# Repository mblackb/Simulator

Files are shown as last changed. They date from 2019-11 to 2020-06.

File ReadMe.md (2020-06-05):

# Documentation for Elcano Simulator Code

**UW Bothell, 2020**

**Advisor :** *Tyler Folsom*

**Team 2019:** *Zach Gale, Jonah Lim, Matthew Moscola, Francisco Navarro-Diaz*

**Team 2020:** *Colton Sellers, Brandon Thompson, Mariah Files, Will Song, Launnie Ginn*

## Purpose
The following is a generalized list of the desired functionality of the simulator.
 - Simulate data for all sensors associated with Elcano Trike.
 - Simulate Elcano behavior to throttle, brake, and steering.
 - Have low and high-level boards function normally with the simulated sensor data without knowing data is being simulated.
 - Allow low and high-level board interaction to be tested.
 - Allow autonomous driving to be tested.
 
## Components ##

#### Simulation:
Code to be executed by a computer that has access to a Carla server, either locally, or through a network.  Controls all objects in Carla simulation.  Sends data to routerboard via client.  Also retrieves actuation instructions from the router board and sends to Carla to control the vehicle.

#### Router Board:
Code to be executed on the Arduino Due that functions as the router board.  Routes drive commands from low-level to Carla.  Also routes sensor data from Carla to high/low-level boards.

## How to Set-Up ##
The following is a guide to set up the Elcano simulator.

#### Materials: 
- 2 Arduino Due. (1 with High-Level Code, 1 with router board code)
- 1 Low-level board with Arduino Mega 2560.
- 1 Router board PCB (Schematics Included, created for Elcano Project)
- 1 male to female DB15 ribbon cable.
- 2 USB A male to USB Micro B male cables.
- 1 USB A male to B male cable.
- 1 computer running Carla 0.9.8 (Can run locally, for development we do this)
- 1 computer to interface between Carla client (Our Simulation Client) and router board (Using Due Router Board Programming Port)

#### To get the Repo as well as submodules (High level and Low level code)
Use git in a shell to clone the repo into a directory using the options below
OR
Just download the repo as zip and unpack (Ensure you have the high level and low level code in the arduino dir)

#### Option 1: clone, then update submodules (If you don't need the arduino code, just clone)
git clone https://github.com/C-SELLERS/Simulator

cd .\Simulator\

git submodule init

git submodule update

#### Option 2: Get repo and recursively get submodules
git clone https://github.com/C-SELLERS/Simulator --recursive

#### Arduino Preparation (If uploading arduino code)
Libraries needed are listed below:

- CAN_BUS_SHIELD by Seeed-Studio
  - [https://github.com/Seeed-Studio/CAN_BUS_Shield](https://github.com/Seeed-Studio/CAN_BUS_Shield)
- PID by Brett Beauregard
  - [https://github.com/br3ttb/Arduino-PID-Library](https://github.com/br3ttb/Arduino-PID-Library)
- Pin Change Interrupt by Nico Hood
  - [https://github.com/NicoHood/PinChangeInterrupt](https://github.com/NicoHood/PinChangeInterrupt)
- MCP48x2 DAC by Jonas Forsberg
  - [https://github.com/SweBarre/MCP48x2](https://github.com/SweBarre/MCP48x2).
- Arduino Due Timer Interrupts by Ivan Seidel
  - [https://github.com/ivanseidel/DueTimer](https://github.com/ivanseidel/DueTimer)

Then connect each arduino and upload the respective code to each board. 
   - HighLevel (./Arduino/HighLevel/) code to Arduino Mega (Right side of Router PCB)
   - LowLevel (./Ardunio/LowLevel/) code to Arduino Due (Left side of Router PCB)
   - Routerboard (./Arduino/Router_Board_v1) code to Arduino Due (Middle of Router PCB)

NOTE: PORTS ARE IMPORTANT ON ROUTERBOARD DUE
  - Programming port is used to upload code and debug via serial monitor
  - Native port is used to communicate with CARLA

#### Python Requirements:
- Have Python 3 Installed, we use (3.7.6)
- In a terminal move to .\Simulation\
- run: pip3 install -r requirements.txt
- Pip will install all the required python libraries for the simulator

#### Start Simulation:
- Make sure Carla is running either locally or somewhere accessible over the network
- If not already, have routerboard due plugged in via native port
- Start Simulator UI by running start.bat (.\Simulation\start.bat)
- By default it will populate local running Carla settings, if using a network based server enter IP and Port of Carla into the respective boxes. (i.e. 192.168.1.1, 2010)
- For control via Elcano leave mode as Auto, to control via manual keyboard input change mode to Manual.
- Click "Connect to CARLA"
   - If Auto mode, it will pop up selection of COM devices, select routerboard native port COM to begin and press go. (Will add path selection in the future???)
   - If Manual mode, client will start with keyboard controls (WASD) 

You did it!! Good job. :)

## Out of Scope Functionality Tested/Implemented ##
- Our project required us to delve into pieces of code within the Elcano project outside of our scope.  Understanding of how sensors are read by the high and low-level boards is necessary for the simulation of the sensors.  We were able to fix some issues regarding the CAN communication between the high and low-level boards.  The modified low-level code was not pushed to the main low-level code folder in the repository on Github, however, it is included within the simulator documentation.  The following were implemented.
- Unification of the proposed CAN message structure and the actual CAN message processing on the low-level code for CAN messages with ID 0x350 (High-level drive instructions).  These are CAN messages the high-level will send to the low level to facilitate autonomy.
- Fixing the DAC output voltage by using the MCP48x2 library by Jonas Forsberg.

## To Do (Software): ##
#### High Priority:
- Simulate gyro sensor
- Simulate accelerometer/magnetometer sensor.
- Simulate wheel angle sensor.
- Implement steering actuation when low-level CAN processing of steering command is fixed.
- Initialize CAN with high-level board code and incorporate in demo instead of separate CAN transceiver.
#### Medium Priority:
- Simulate ScanseSweep.
- Implement receiver board when board is fully fixed.
- Incorporate Elcano trike physics to simulated vehicle.
#### Low Priority

## Bugs
- While we were able to fix the code for the low-level CAN interpretation of the throttle and brake commands from high-level CAN messages, the PWM steering response was not fully tested.  We were unable to get the low-level board to output the correct PWM for the sent CAN messages and this needs more testing.
- The receiver board cannot get CAN to initialize.  Voltage testing confirmed that the CAN components (MCP2515 and MCP 2550) are receiving the correct operating voltages (5v).  Also, multiple CAN libraries besides the suggested Seeed Studio library were tested with no success (SparkFun CAN library was one of the tested libraries).  Possible problem is incompatibility between the 5v CAN components and the 3.3V SAMD21 board.  Another possible problem is design flaw of pcb.
- Low-level processing of CAN messages for ID 0x350 is faulty.  Bit shifting and produced output do not match the CAN guidelines on the wiki.  This was fixed in the low-level code included in the simulator folder but not pushed to the Elcano Github repository.

## Note:
- In PowerShell, in CarlaUE4 path, run Carla as: ***Start-Process CarlaUE4 -ArgumentList “—quality-level=Low”*** to lower gpu load.
- Headless mode can be enabled for complete removal of graphics rendering, however, visual debugging is extremely useful.

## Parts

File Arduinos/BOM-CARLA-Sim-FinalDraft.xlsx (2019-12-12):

Part
Build Qty | Unit Price | Order Qty | Ext Price | Value | Device | Package | Parts | Description | DigiKey Part Number | Manufactorer Number | URL
1 | $1.60 | 10 | $11.21 |  | CONN_04SCREW | SCREWTERMINAL-3.5MM-4 | J1 | Multi connection point. Oft | WM7860-ND | 393570004 | https://www.digikey.com/products/en?keywords=WM7860-ND
1 |  |  |  |  | JP1E | JP1 | JP1 | JUMPER
2 | $1.15 | 10 | $11.50 |  | LED3MM | LED3MM | DEBUG, POWER_OK | LED | 97K4090 | L23R3000K2P2 | https://www.newark.com/multicomp/l23r3000k2p2/led-3mm-green-yellow/dp/97K4090?mckv=sFNQmY5rU_dc|pcrid|350577457110|plid||kword||match||slid||product|97K4090|pgrid|69832101039|ptaid|pla-364360548877|&CMP=KNC-GUSA-GEN-SHOPPING-Private-LabelMulticomp-NonShowcasing
1 | - | In House | - | PINHD-1X6 | PINHD-1X6 | 1X06 | POWER | PIN HEADER
1 | - | 6NOV ORDER | - | MCP2515 | MCP2515(MCP2510)P | DIP18 | IC1_2515 | CAN controller with SPI int | MCP2515-I/P-ND | MCP2515-I/P | https://www.digikey.com/products/en?keywords=MCP2515-I%2FP-ND
5 | - | 6NOV ORDER | - | 0.1uF | C-USC1206 | C1206 | C10, C11, C12, C13, C14 | CAPACITOR, American symbol | 493-10420-1-ND | UMA1H0R1MCD2TP | https://www.digikey.com/products/en?keywords=493-10420-1-ND
2 | $0.10 | 10 | $0.40 | 100 | R-US_R1206 | R1206 | R7, R8 | RESISTOR, American symbol | CR1206-FX-1000ELFCT-ND | CR1206-FX-1000ELF | https://www.digikey.com/product-detail/en/bourns-inc/CR1206-FX-1000ELF/CR1206-FX-1000ELFCT-ND/3437916
1 | $0.14 | 10 | $1.00 | 100n | C-EU0603-RND | C0603-ROUND | C2 | CAPACITOR, European symbol | 399-1097-1-ND | C0603C104J4RACTU | https://www.digikey.com/product-detail/en/kemet/C0603C104J4RACTU/399-1097-1-ND/411372?slid=
1 | $0.39 | 10 | $3.25 | 16MHz | ECS-160-20-46X | XTAL_ECS-160-20-46X | Q1 | QUARTZ CRYSTAL T/H | XC1759-ND | ECS-160-20-46X | https://www.digikey.com/product-detail/en/ecs-inc/ECS-160-20-46X/XC1759-ND/2676589
3 | $0.10 | 10 | $0.88 | 1K | R-US_R1206 | R1206 | R5, R12, R13 | RESISTOR, American symbol | CR1206-JW-102ELFCT-ND (https://www.digikey.com/product-detail/en/bourns-inc/CR1206-JW-102ELF/CR1206-JW-102ELFCT-ND/3925455) | CR1206-JW-102ELF | https://www.digikey.com/product-detail/en/bourns-inc/CR1206-JW-102ELF/CR1206-JW-102ELFCT-ND/3925455
2 | $0.10 | 10 | $0.42 | 2.2K | R-US_R1206 | R1206 | R22, R24 | RESISTOR, American symbol | CR1206-FX-2201ELFCT-ND (https://www.digikey.com/product-detail/en/bourns-inc/CR1206-FX-2201ELF/CR1206-FX-2201ELFCT-ND/3767688) | CR1206-FX-2201ELF | https://www.digikey.com/product-detail/en/bourns-inc/CR1206-FX-2201ELF/CR1206-FX-2201ELFCT-ND/3767688
1 | $0.10 | 10 | $0.40 | 20K | R-US_R1206 | R1206 | R14 | RESISTOR, American symbol | CR1206-FX-2002ELFCT-ND (https://www.digikey.com/product-detail/en/bourns-inc/CR1206-FX-2002ELF/CR1206-FX-2002ELFCT-ND/3767632) | CR1206-FX-2002ELF | https://www.digikey.com/product-detail/en/bourns-inc/CR1206-FX-2002ELF/CR1206-FX-2002ELFCT-ND/3767632
1 | - | In House | - | 2x3 | PINHD-2X3 | 2X03 | ICSP | PIN HEADER
2 | $0.12 | 10 | $1.08 | 3.3K | R-US_R1206 | R1206 | R23, R25 | RESISTOR, American symbol | CR1206-FX-3301ELFCT-ND (https://www.digikey.com/product-detail/en/bourns-inc/CR1206-FX-3301ELF/CR1206-FX-3301ELFCT-ND/3767770) | CR1206-FX-3301ELF | https://www.digikey.com/product-detail/en/bourns-inc/CR1206-FX-3301ELF/CR1206-FX-3301ELFCT-ND/3767770
2 | $0.10 | 10 | $0.15 | 33pF | C-USC1206 | C1206 | C5, C6 | CAPACITOR, American symbol | 311-1586-1-ND (https://www.digikey.com/product-detail/en/yageo/CC0201JRNPO9BN330/311-1586-1-ND/5195488) | CC0201JRNPO9BN330 (https://www.digikey.com/product-detail/en/yageo/CC0201JRNPO9BN330/311-1586-1-ND/5195488) | https://www.digikey.com/product-detail/en/yageo/CC0201JRNPO9BN330/311-1586-1-ND/5195488
4 | $0.14 | 50 | $5.30 | 4.7K | R-US_0204/7 | 0204/7 | R1, R2, R3, R4 | RESISTOR, American symbol | MBA02040C4701FRP00 (https://www.mouser.com/ProductDetail/Vishay-Beyschlag/MBA02040C4701FRP00) | 594-5063JD4K700FT | https://www.mouser.com/ProductDetail/Vishay-Beyschlag/MBA02040C4701FRP00
1 | $0.10 | 10 | $0.89 | 4.7K | R-US_R1206 | R1206 | R9 | RESISTOR, American symbol | CR1206-JW-472ELFCT-ND | CR1206-JW-472ELF | https://www.digikey.com/product-detail/en/bourns-inc/CR1206-JW-472ELF/CR1206-JW-472ELFCT-ND/3925468
2 | $0.91 | 10 | $5.78 | 47u | CPOL-EUD | PANASONIC_D | PC1, PC2 | POLARIZED CAPACITOR, Europe | 667-EEE-FK1H470XV | EEE-FK1H470XV (https://www.mouser.com/ProductDetail/Panasonic/EEE-FK1H470XV) | https://www.mouser.com/ProductDetail/Panasonic/EEE-FK1H470XV
2 | $1.15 | 10 | $8.13 | 560pF | C-USC1206 | C1206 | C7, C8 | CAPACITOR, American symbol | 80-C1206C561JBG | C1206C561JBGACTU (https://www.digikey.com/product-detail/en/murata-electronics/GRM0335C1E561JA01D/490-14862-1-ND/6624019) | https://www.mouser.com/ProductDetail/KEMET/C1206C330JGGACAUTO
1 | - | In House | - | Analog In | PINHD-1X8 | 1X08 | ADCL | PIN HEADER | - | -
1 | - | In House | - | Analog In | PINHD-1X8 | 1X08 | ADCH | PIN HEADER | - | -
1 | $0.58 | 10 | $5.43 | PJ-037A | PJ-037A |  | X1 | DC Barrel Power Jack |  | PJ-037A | https://www.digikey.com/product-detail/en/cui-devices/PJ-037A/CP-037A-ND/1644545
2 | - | - | - | DUE(NORMAL) | DUE(NORMAL) | DUE(NORMAL) | MCU2, MCU3 |  | - | -
1 | - | - | - | Digital 0 | PINHD-1X8 | 1X08 | DIGITAL_0-7 | PIN HEADER | - | -
1 | - | In House | - | Digital 1 | PINHD-1X8 | 1X08 | DIGITAL_14-21 | PIN HEADER | - | -
1 | - | - | - | Digital 2 | PINHEAD_PINHD-2X18 | PINHEAD_2X18 | MEGA_EXPANSION | PIN HEADER | - | -
1 | - | - | - | Digital 8 | PINHD-1X10 | 1X10 | DIGITAL_8-13 | PIN HEADER | - | -
2 | $0.61 | 10 | $5.37 | LLSHIFTER | ELSHIFTER | ELSHIFTER | U1, U2 | TXB0108 LEVEL SHIFTER. Foot | 296-16845-1-ND | SN74LVC2T45DCTR | https://www.digikey.com/product-detail/en/texas-instruments/SN74LVC2T45DCTR/296-16845-1-ND/639461
1 | $0.25 | 5 | $1.25 | M7 | DIODE-SMB | SMB | D1 | DIODE | - | COM-14884 | https://www.sparkfun.com/products/14884
1 | $0.81 | 10 | $7.14 | MC33269D- | MC33269D-5.0 | DPACK | IC2 | Adjustable Output Low Dropo | MC33269D-5.0GOS-ND | MC33269D-5.0G | https://www.digikey.com/product-detail/en/on-semiconductor/MC33269D-5.0G/MC33269D-5.0GOS-ND/919039
1 | $0.90 | 10 | $7.94 | MC33269ST | MC33269ST-3.3T3 | SOT223 | IC1 | Adjustable Output Low Dropo | MC33269ST-3.3T3GOSCT-ND | MC33269ST-3.3T3G | https://www.digikey.com/product-detail/en/on-semiconductor/MC33269ST-3.3T3G/MC33269ST-3.3T3GOSCT-ND/2120818
1 | - | 6NOV ORDER | - | MCP2551DI | MCP2551DIL08 | IC-PACKAGE_DIL08 | IC2_2551 | CAN transceiver | MCP2551-I/P-ND | MCP2551-I/P | https://www.digikey.com/product-detail/en/microchip-technology/MCP2551-I-P/MCP2551-I-P-ND/509453
1 | $1.48 | 25 | $30.75 | MCP4802 | DIL8 | DIL08 | IC3_4802 | Dual In Line / Socket | MCP4802-E/P-ND | MCP4802-E/P | https://www.digikey.com/product-detail/en/microchip-technology/MCP4802-E-P/MCP4802-E-P-ND/2332807
1 | $0.36 | 10 | $2.95 | PESD1CAN | PESD1CAN | SPARKFUN-DISCRETESEMI_SOT23-3 | D4 | CAN bus ESD protection diod | 1727-1306-1-ND | PESD1CAN-UX | https://www.digikey.com/product-detail/en/nexperia-usa-inc/PESD1CAN-UX/1727-1306-1-ND/4386316

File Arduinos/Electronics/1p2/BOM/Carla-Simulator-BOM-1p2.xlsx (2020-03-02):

Item Number | BUILD-OPT | Quantity | Part Reference | Description | MF | MP | PACKAGE | Value | DIGI-KEY_PART_NUMBER | DIGI-KEY_PURCHASE_URL | DIGI-KEY_PRICE | Extended Quantity | Extended Price
1 | ALL | 1 | C2 | CAP CER 0.1UF 16V X7R 0603 | KEMET | C0603C104J4RACTU | 0603 | 100n | 399-1097-1-ND | https://www.digikey.com/products/en?keywords=399-1097-1-Nd | $0.15 | 36 | $5.40
2 | ALL | 2 | C5 C6 | CAP CER 33PF 50V C0G/NPO 1206 | Yageo | CC1206JRNPO9BN330 | 1206 | 33pF | 311-1156-1-ND | https://www.digikey.com/product-detail/en/yageo/CC1206JRNPO9BN330/311-1156-1-ND/303066 | $0.24 | 72 | $17.28
3 | ALL | 2 | C7 C8 | CAP CER 1206 33PF 2000V C0G 5% | KEMET | C1206C330JGGACAUTO | 1206 | 560pF | 399-16703-1-ND | https://www.digikey.com/product-detail/en/kemet/C1206C330JGGACAUTO/399-16703-1-ND/8110069 | $1.06 | 72 | $76.32
4 | ALL | 7 | C10 C11 C12 C13 C14 C15 C16 | CAP CER 0.1UF 50V X7R 1206 | KEMET | C1206C104K5RAC7800 | 1206 | 0.1uF | 399-C1206C104K5RAC7800CT-ND | https://www.digikey.com/product-detail/en/kemet/C1206C104K5RAC7800/399-C1206C104K5RAC7800CT-ND/411524 | $0.12 | 252 | $30.24
5 | ALL | 1 | C17 | CAP CER 4700PF 50V NP0 1206 | TDK Corporation | CGA5C2NP01H472J060AA | 1206 | 4700pF | 445-12840-1-ND | https://www.digikey.com/product-detail/en/tdk-corporation/CGA5C2NP01H472J060AA/445-12840-1-ND/3954506 | $0.43 | 36 | $15.48
6 | ALL | 1 | D1 | DIODE SCHOTTKY 60V 5A SMB | STMicroelectronics | STPS5L60U | DO-214AA | M7 | 497-16321-1-ND | https://www.digikey.com/product-detail/en/stmicroelectronics/STPS5L60U/497-16321-1-ND/5848347 | $0.59 | 36 | $21.24
7 | ALL | 1 | D4 | TVS DIODE 24V 50V SC70-3 | Nexperia USA Inc. | PESD1CAN-UX | SC-70 | PESD1CAN | 1727-1306-1-ND | https://www.digikey.com/product-detail/en/nexperia-usa-inc/PESD1CAN-UX/1727-1306-1-ND/4386316 | $0.39 | 36 | $14.04
8 | ALL | 2 | DS1 DS2 | LED, Green, Yellow, Through Hole, T-1 (3mm), 118 °, Round, Y 30mA, G 30mA | Multicomp | L23R3000K2P2 | 2-TH | N_A | 97K4090 | https://www.newark.com/multicomp/l23r3000k2p2/led-3mm-green-yellow/dp/97K4090?mckv=sFNQmY5rU_dc|pcrid|350577457110|plid||kword||match||slid||product|97K4090|pgrid|69832101039|ptaid|pla-364360548877|&CMP=KNC-GUSA-GEN-SHOPPING-Private-LabelMulticomp-NonShowcasing | $1.44 | 72 | $103.68
9 | ALL | 1 | IC1 | IC REG LINEAR 3.3V 800MA SOT223 | ON Semiconductor | MC33269ST-3.3T3G | SOT-223 | MC33269ST-3.3T3G | MC33269ST-3.3T3GOSCT-ND | https://www.digikey.com/product-detail/en/on-semiconductor/MC33269ST-3.3T3G/MC33269ST-3.3T3GOSCT-ND/2120818 | $0.93 | 36 | $33.48
10 | ALL | 1 | IC1_2515 | IC CAN CONTROLLER W/SPI 18DIP | Microchip Technology | MCP2515-I/P | 18-PDIP | MCP2515 | MCP2515-I/P-ND | https://www.digikey.com/products/en?keywords=MCP2515-I%2FP-ND | $1.94 | 36 | $69.84
11 | ALL | 1 | IC2 | IC REG LINEAR 5V 800MA DPAK | ON Semiconductor | MC33269DTRK-5.0G | DPAK | MC33269DT-5.0G | MC33269DTRK-5.0GOSCT-ND | https://www.digikey.com/product-detail/en/on-semiconductor/MC33269DTRK-5.0G/MC33269DTRK-5.0GOSCT-ND/2120817 | $0.74 | 36 | $26.64
12 | ALL | 3 | IC2_2551 IC3_2551 IC4_2551 | IC TRANSCEIVER HALF 1/1 8DIP | Microchip Technology | MCP2551-I/P | 8-PDIP | MCP2551DIL08 | MCP2551-I/P-ND | https://www.digikey.com/product-detail/en/microchip-technology/MCP2551-I-P/MCP2551-I-P-ND/509453 | $1.09 | 108 | $117.72
13 | ALL | 1 | IC3_4802 | IC DAC 8BIT V-OUT 8DIP | Microchip Technology | MCP4802-E/P | 8-PDIP | MCP4802 | MCP4802-E/P-ND | https://www.digikey.com/product-detail/en/microchip-technology/MCP4802-E-P/MCP4802-E-P-ND/2332807 | $1.48 | 36 | $53.28
14 | ALL | 1 | J1 | TERM BLK 4POS SIDE ENT 3.5MM PCB | Molex | 393570004 | 4-TH | N_A | WM7860-ND | https://www.digikey.com/products/en?keywords=WM7860-ND | $1.60 | 36 | $57.60
15 | ALL | 1 | J2 | CONN HEADER VERT 20POS 2.54MM | TE Connectivity | 5103308-5 | 2x10-TH | PicoScope | A33165-ND | https://www.digikey.com/products/en?keywords=A33165-ND | $1.54 | 36 | $55.44
16 | ALL | 1 | JP2 | CONN HEADER VERT 6POS 2.54MM | Amphenol ICC (FCI) | 67997-206HLF | 2x3-TH | PINHD-2X3 | 609-3234-ND | https://www.digikey.com/product-detail/en/amphenol-icc-fci/67997-206HLF/609-3234-ND/1878491 | $0.33 | 36 | $11.88
18 | ALL | 2 | PC1 PC2 | Aluminum Electrolytic Capacitors - SMD 50VDC 47uF 20% Anti-Vibe AEC-Q200 | Panasonic | EEE-FK1H470XV | SMD | 47u | 667-EEE-FK1H470XV | https://www.mouser.com/ProductDetail/Panasonic/EEE-FK1H470XV | $0.91 | 72 | $65.52
19 | ALL | 1 | Q1 | Crystal 16MHz _30ppm _Tol_ _50ppm _Stability_ 20pF FUND 50Ohm | ECS Inc. | ECS-160-20-46X | HC-46/X | 16MHz | XC1759-ND | https://www.digikey.com/products/en?keywords=XC1759-ND | $0.39 | 36 | $14.04
20 | ALL | 4 | R1 R2 R3 R4 | Metal Film Resistors .4watt 4.7Kohms 1% 1/8watt body size | Vishay | MBA02040C4701FRP00 | Axial | 4.7 k | 594-5063JD4K700FT | https://www.mouser.com/ProductDetail/Vishay-Beyschlag/MBA02040C4701FRP00 | $0.14 | 144 | $20.16
21 | ALL | 3 | R5 R12 R13 | RES SMD 1K OHM 5% 1/4W 1206 | Bourns Inc. | CR1206-JW-102ELF | 1206 | 1K | 118-CR1206-JW-102ELFCT-ND | https://www.digikey.com/product-detail/en/bourns-inc/CR1206-JW-102ELF/CR1206-JW-102ELFCT-ND/3925455 | $0.10 | 108 | $10.80
22 | ALL | 2 | R7 R8 | RES SMD 100 OHM 1% 1/4W 1206 | Bourns Inc. | CR1206-FX-1000ELF | 1206 | 100 | CR1206-FX-1000ELFCT-ND | https://www.digikey.com/product-detail/en/bourns-inc/CR1206-FX-1000ELF/CR1206-FX-1000ELFCT-ND/3437916 | $0.10 | 72 | $7.20
23 | ALL | 3 | R9 R30 R32 | RES SMD 4.7K OHM 5% 1/4W 1206 | Bourns Inc. | CR1206-JW-472ELF | 1206 | 4.7K | 118-CR1206-JW-472ELFCT-ND | https://www.digikey.com/product-detail/en/bourns-inc/CR1206-JW-472ELF/CR1206-JW-472ELFCT-ND/3925468 | $0.10 | 108 | $10.80
24 | ALL | 1 | R14 | RES SMD 20K OHM 1% 1/4W 1206 | Bourns Inc. | CR1206-FX-2002ELF | 1206 | 20K | CR1206-FX-2002ELFCT-ND | https://www.digikey.com/product-detail/en/bourns-inc/CR1206-FX-2002ELF/CR1206-FX-2002ELFCT-ND/3767632 | $0.10 | 36 | $3.60
25 | ALL | 2 | R22 R24 | RES SMD 2.2K OHM 1% 1/4W 1206 | Bourns Inc. | CR1206-FX-2201ELF | 1206 | 2.2K | CR1206-FX-2201ELFCT-ND | https://www.digikey.com/product-detail/en/bourns-inc/CR1206-FX-2201ELF/CR1206-FX-2201ELFCT-ND/3767688 | $0.10 | 72 | $7.20
26 | ALL | 2 | R23 R25 | RES SMD 3.3K OHM 1% 1/4W 1206 | Bourns Inc. | CR1206-FX-3301ELF | 1206 | 3.3K | CR1206-FX-3301ELFCT-ND | https://www.digikey.com/product-detail/en/bourns-inc/CR1206-FX-3301ELF/CR1206-FX-3301ELFCT-ND/3767770 | $0.11 | 72 | $7.92
30 | ALL | 4 | TP0 TP1 TP3 TP4 | PC TEST POINT COMPACT RED | Keystone Electronics | 5005 | 1-TH | TH_TP | 36-5005-ND | https://www.digikey.com/product-detail/en/keystone-electronics/5005/36-5005-ND/255329 | $0.35 | 144 | $50.40
33 | ALL | 1 | X1 | CONN PWR JACK 2X5.5MM SOLDER | CUI Devices | PJ-037A |  | DC21MMX | CP-037A-ND | https://www.digikey.com/product-detail/en/cui-devices/PJ-037A/CP-037A-ND/1644545 | $0.58 | 36 | $20.88
34 | ALL | 9 | MCU1,MCU2,U1,U2,U3,SD1,SD2 | CONN HEADER VERT 40POS 2.54MM | Sullins | PRPC040SAAN-RC |  |  | S1011EC-40-ND | https://www.digikey.com/product-detail/en/sullins-connector-solutions/PRPC040SAAN-RC/S1011EC-40-ND/2775214 | $0.66 | 324 | $213.84
 |  |  |  |  |  |  |  |  |  |  |  |  | $1141.92
Total Number of boards: |  | 30
Overage |  | 20%

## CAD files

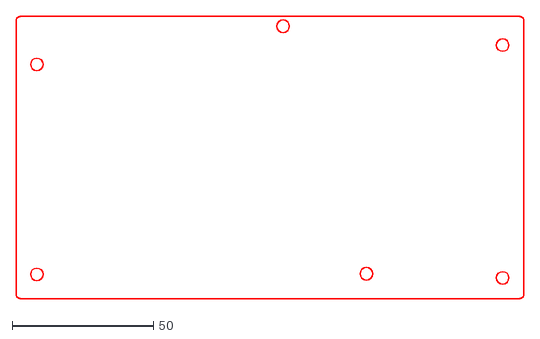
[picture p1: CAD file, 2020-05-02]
Arduinos/Electronics/1p2/Dimensions/Carla_PCB_1p2.dxf
180.0 x 100.0

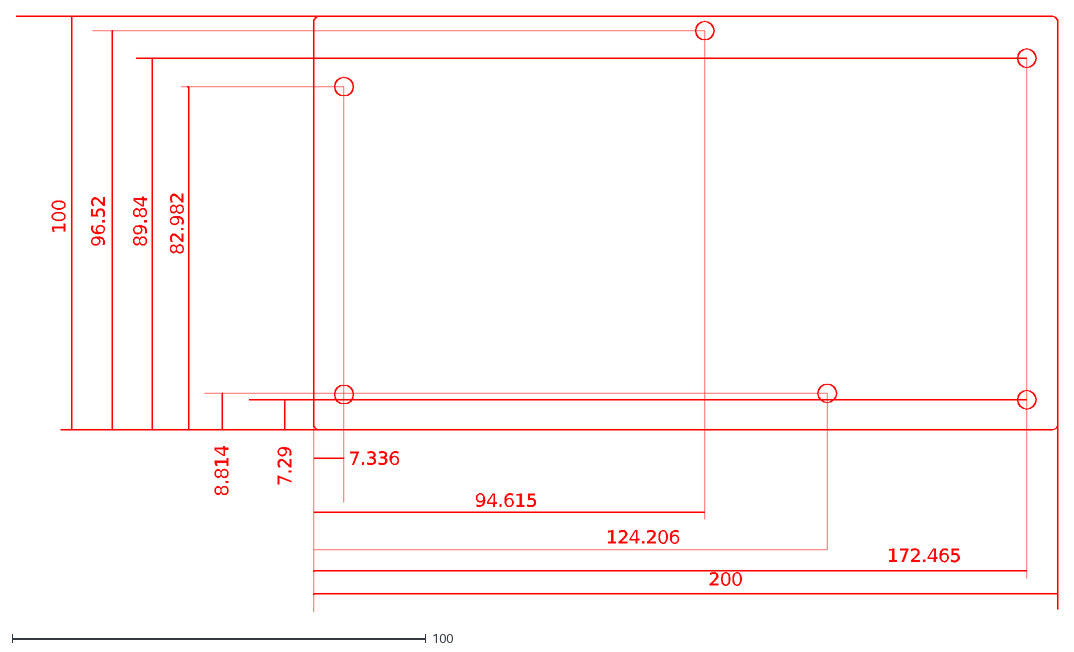
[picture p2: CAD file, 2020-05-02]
Arduinos/Electronics/1p2/Dimensions/Carla_PCB_1p2_Dimensions.dxf
100
96.52
89.84
82.982
8.814
7.29
200
172.465
124.206
94.615
7.336

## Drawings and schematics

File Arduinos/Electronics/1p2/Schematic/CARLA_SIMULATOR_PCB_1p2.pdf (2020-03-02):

# High Level Board

# 1K C⁵ 33pF R² 4.7 k

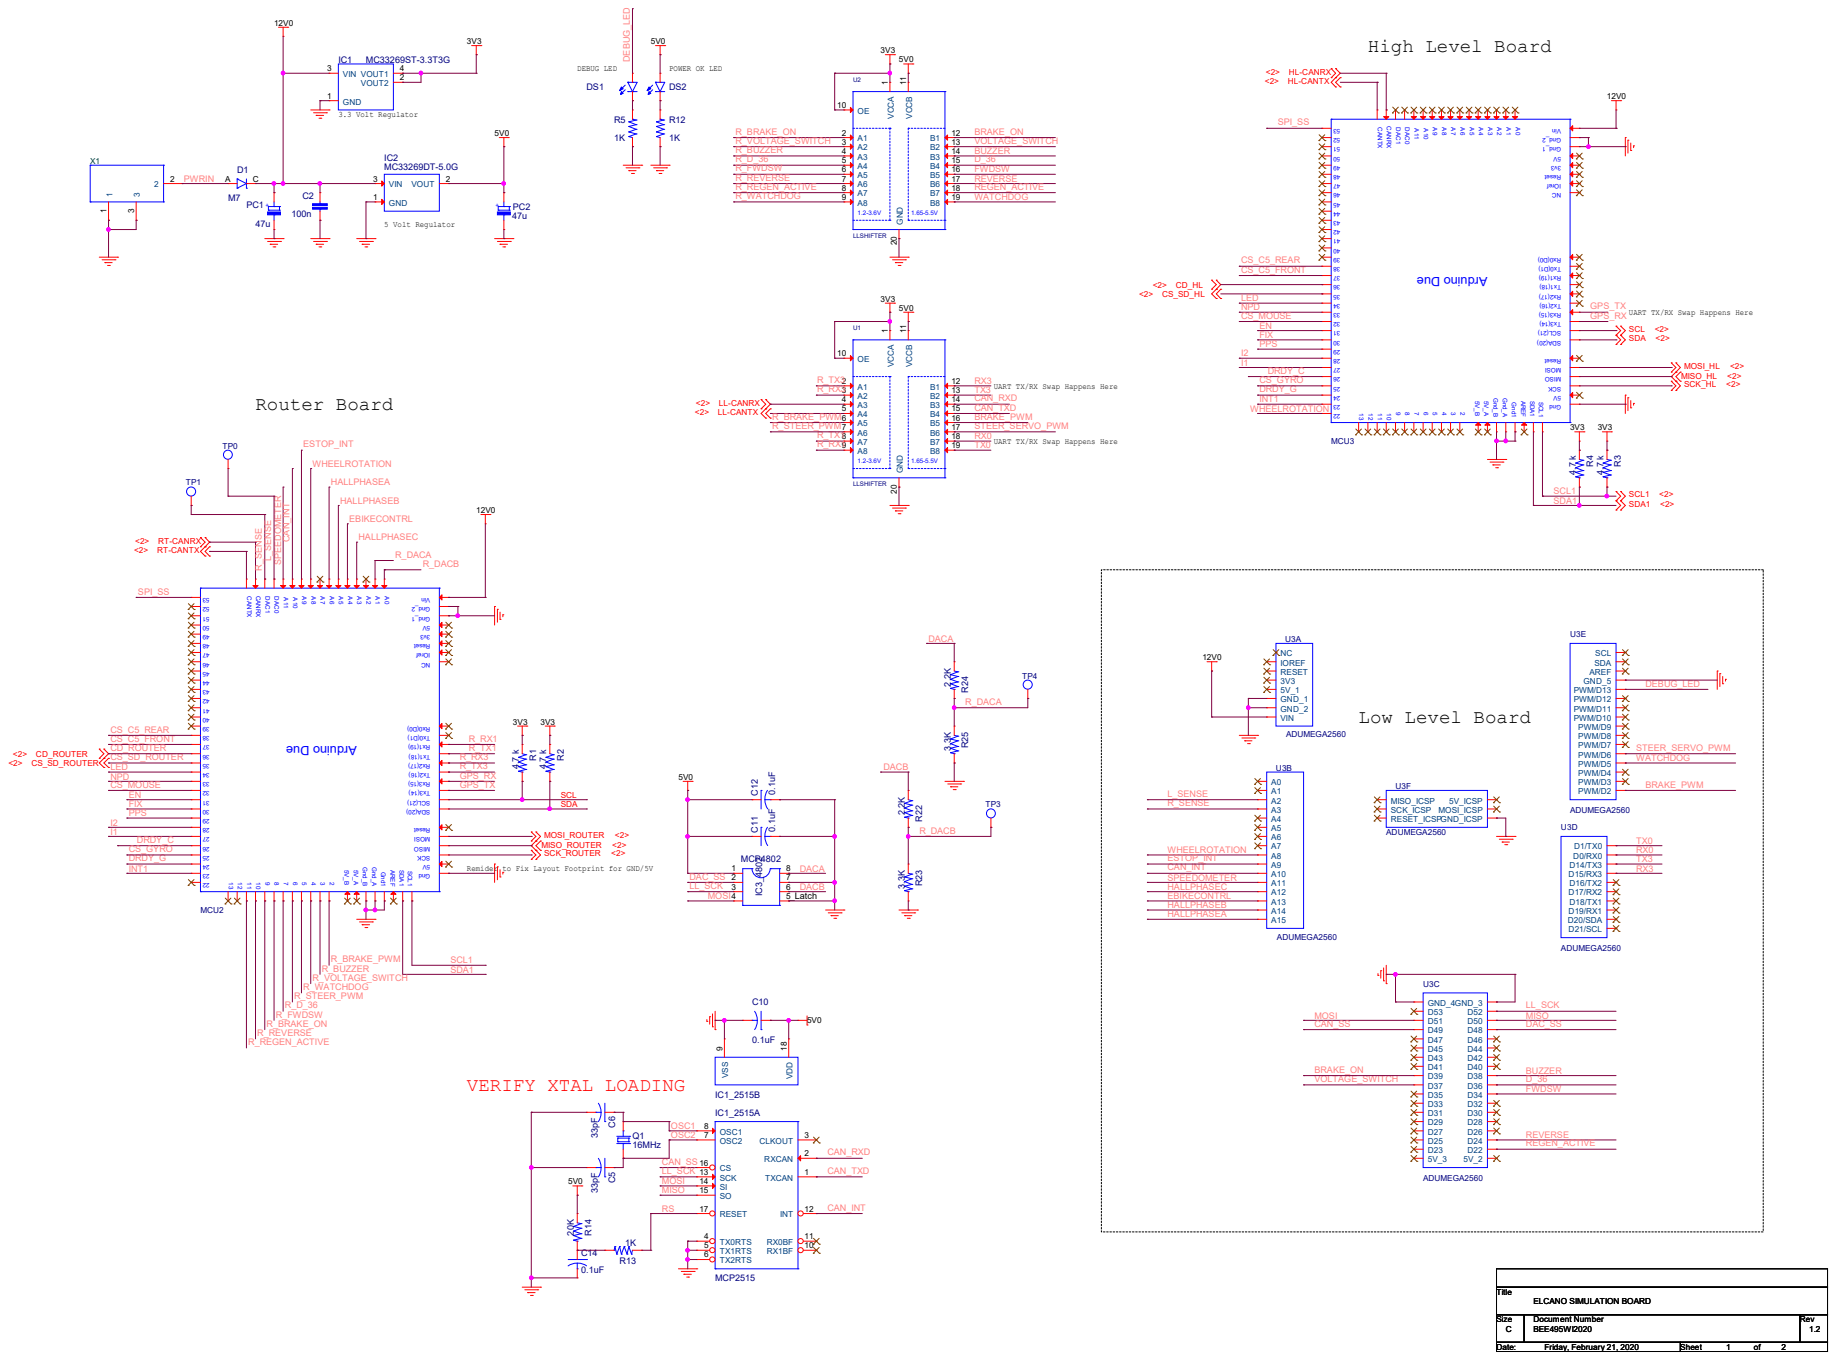
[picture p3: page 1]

UART TX/RX Swap Happens Here

ADUMEGA2560 PWM/D2 PWM/D3 PWM/D4 PWM/D5 PWM/D6 PWM/D7 PWM/D8 PWM/D9 PWM/D10 PWM/D11 PWM/D12 PWM/D13 GND_5 AREF SDA

# Can use either MCP2551 or MCP2561

# 560pF R²⁶60 DNP

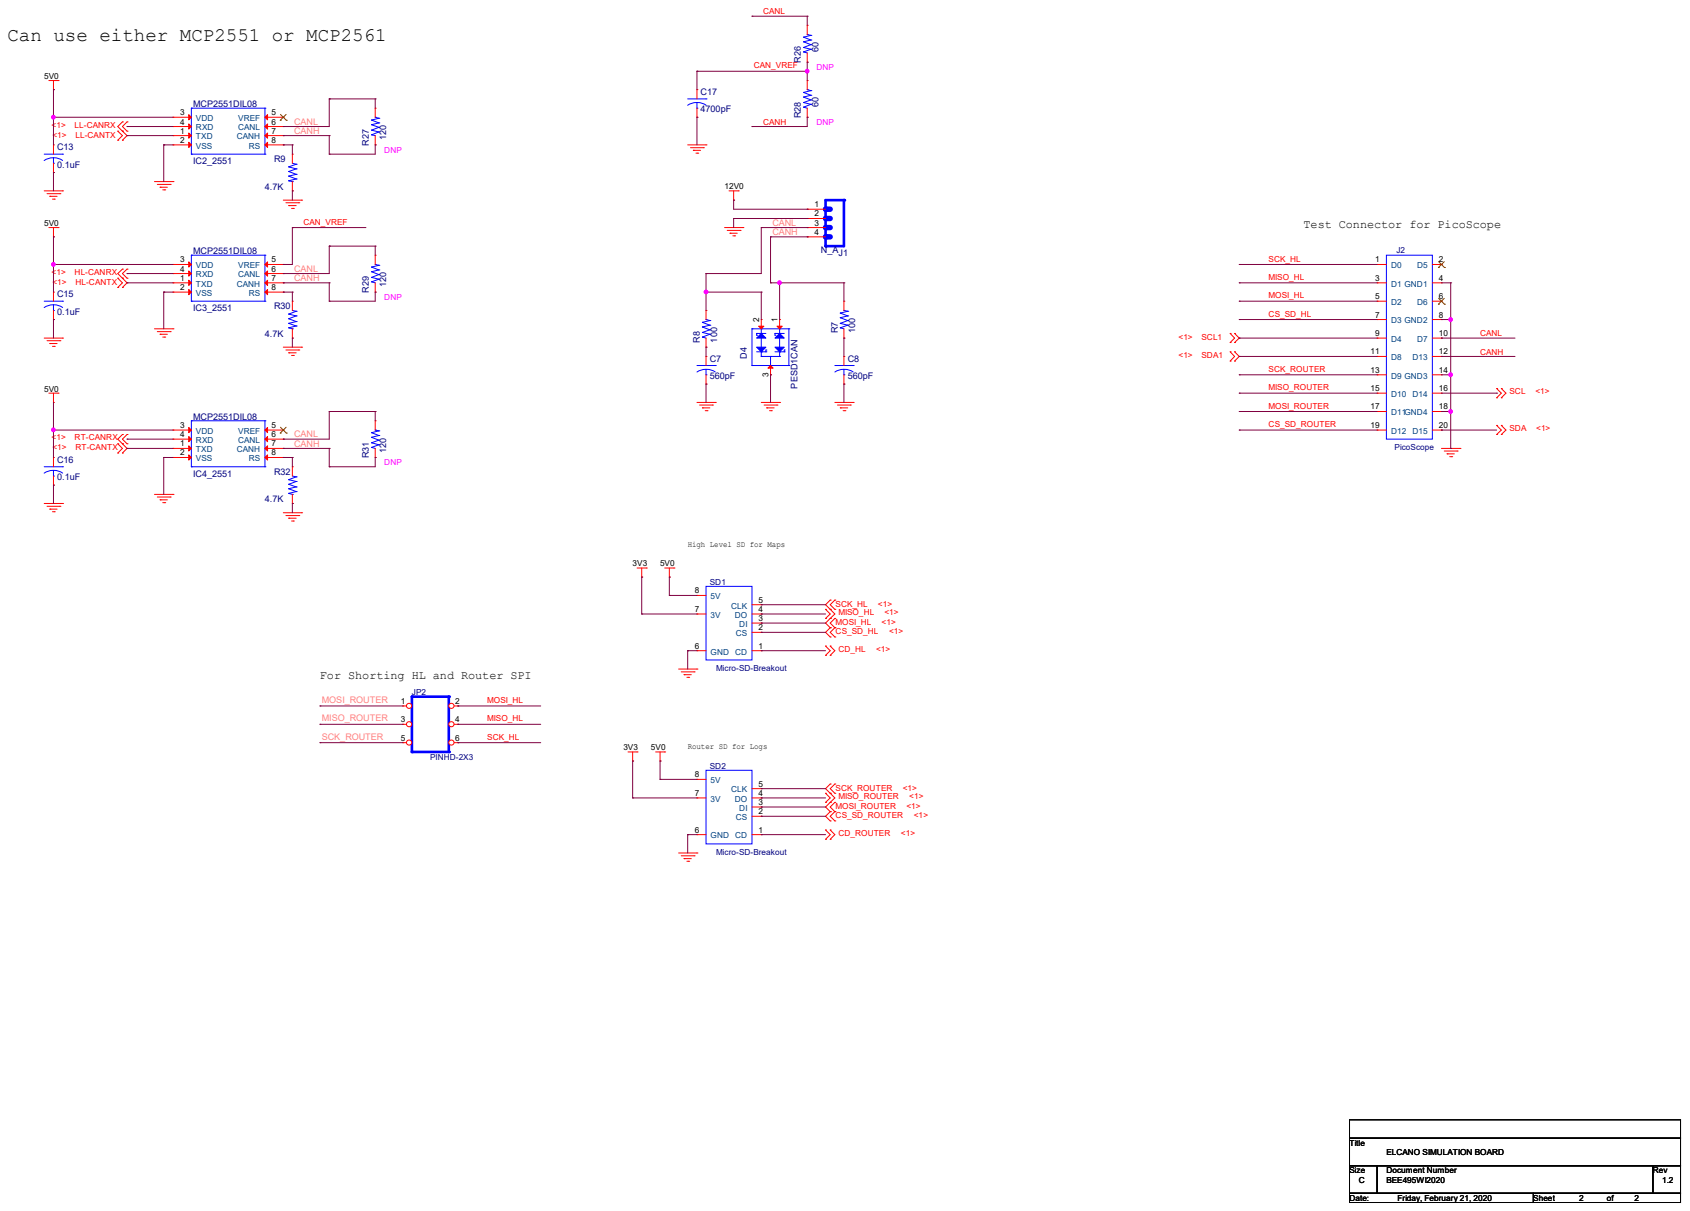
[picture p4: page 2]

Test Connector for PicoScope ¹²V0

High Level SD for Maps

For Shorting HL and Router SPI

Router SD for Logs

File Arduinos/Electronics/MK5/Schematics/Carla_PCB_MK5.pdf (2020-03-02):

# High Level Board

# 1K C⁵ 33pF

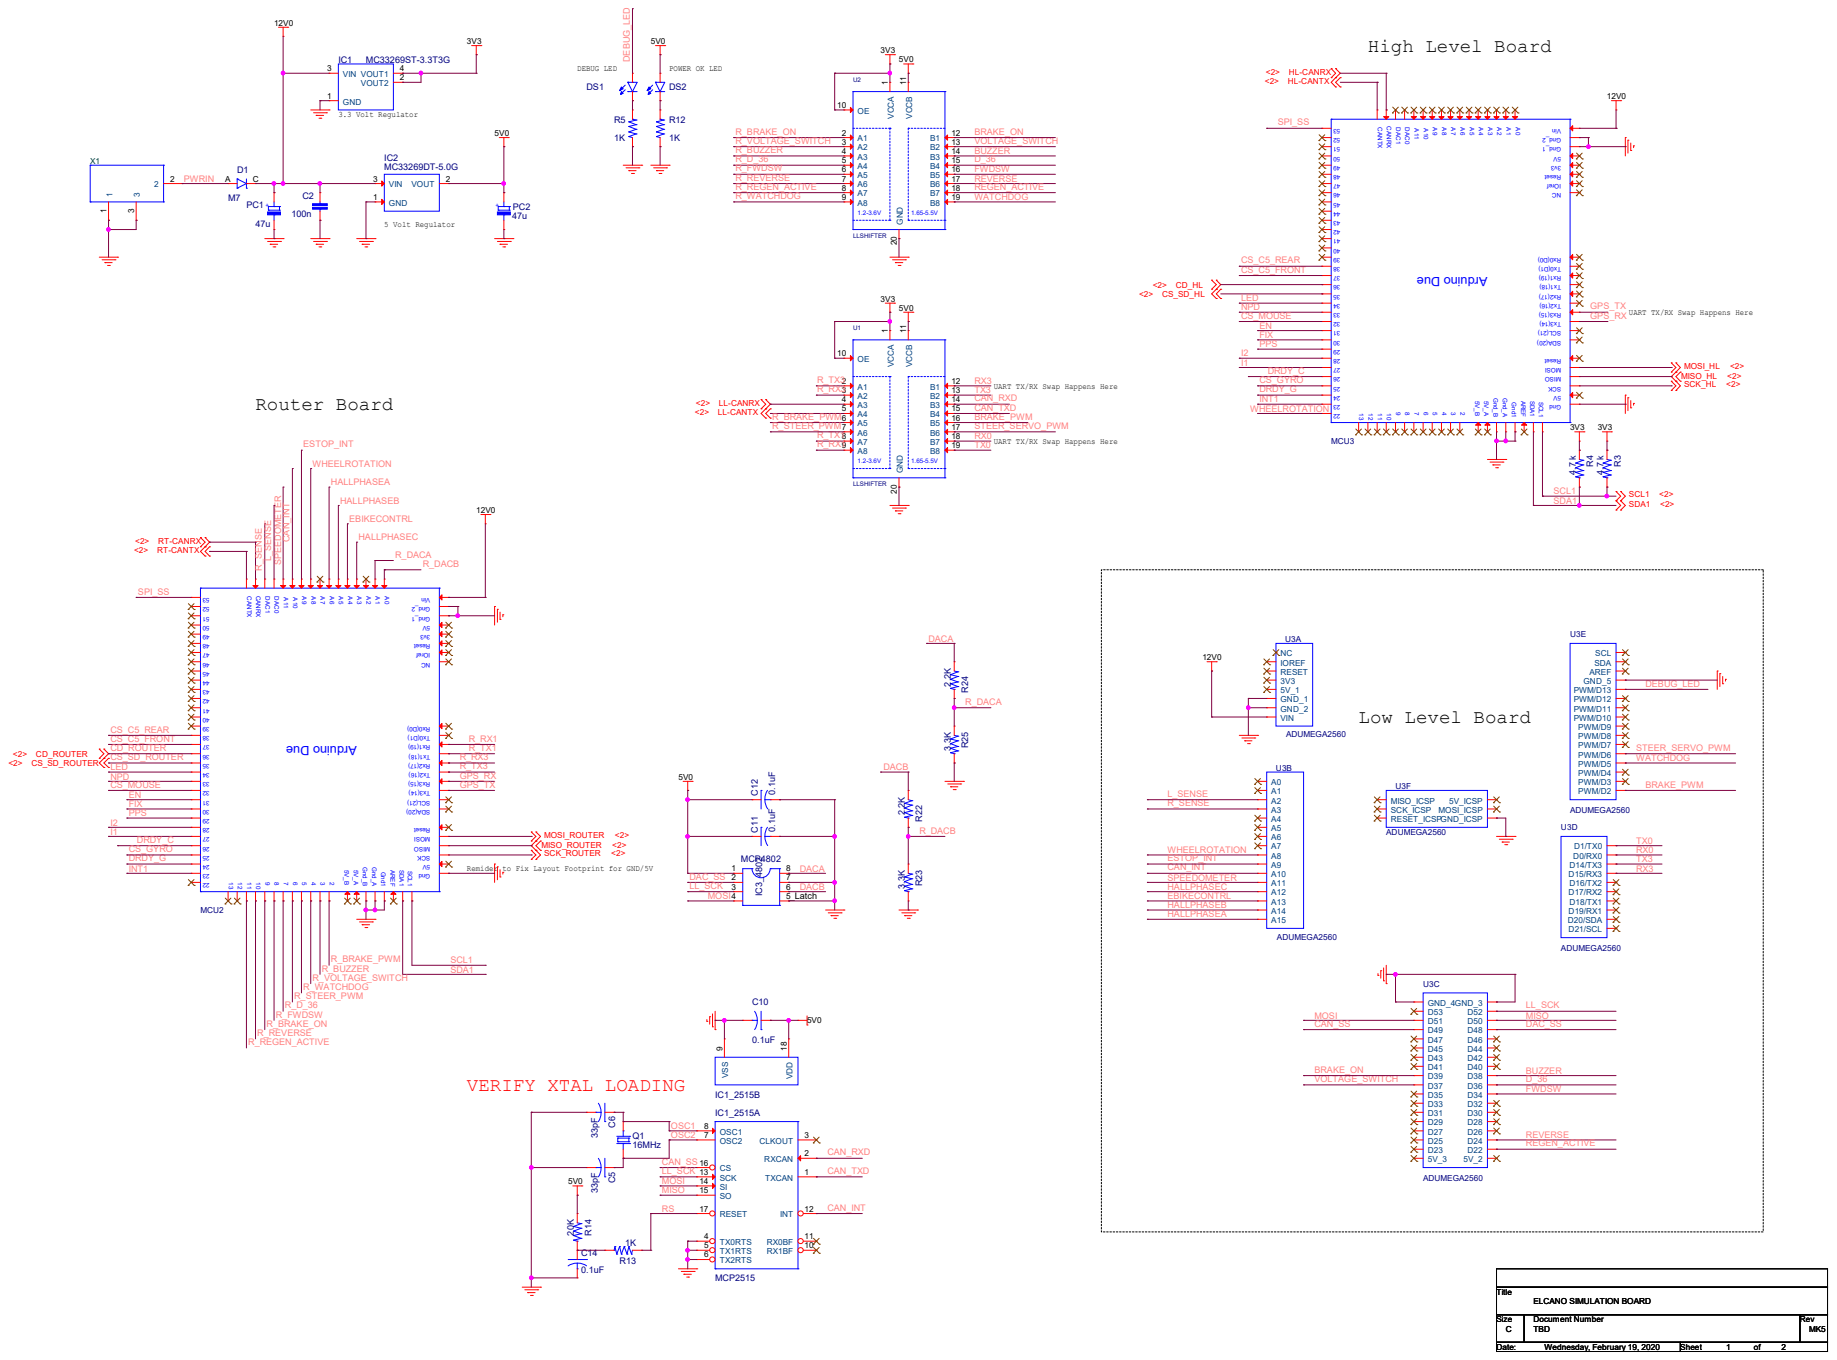
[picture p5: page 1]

UART TX/RX Swap Happens Here

ADUMEGA2560 PWM/D2 PWM/D3 PWM/D4 PWM/D5 PWM/D6 PWM/D7 PWM/D8 PWM/D9 PWM/D10 PWM/D11 PWM/D12 PWM/D13 GND_5 AREF SDA

# Can use either MCP2551 or MCP2561

# 560pF R²⁸60 DNP

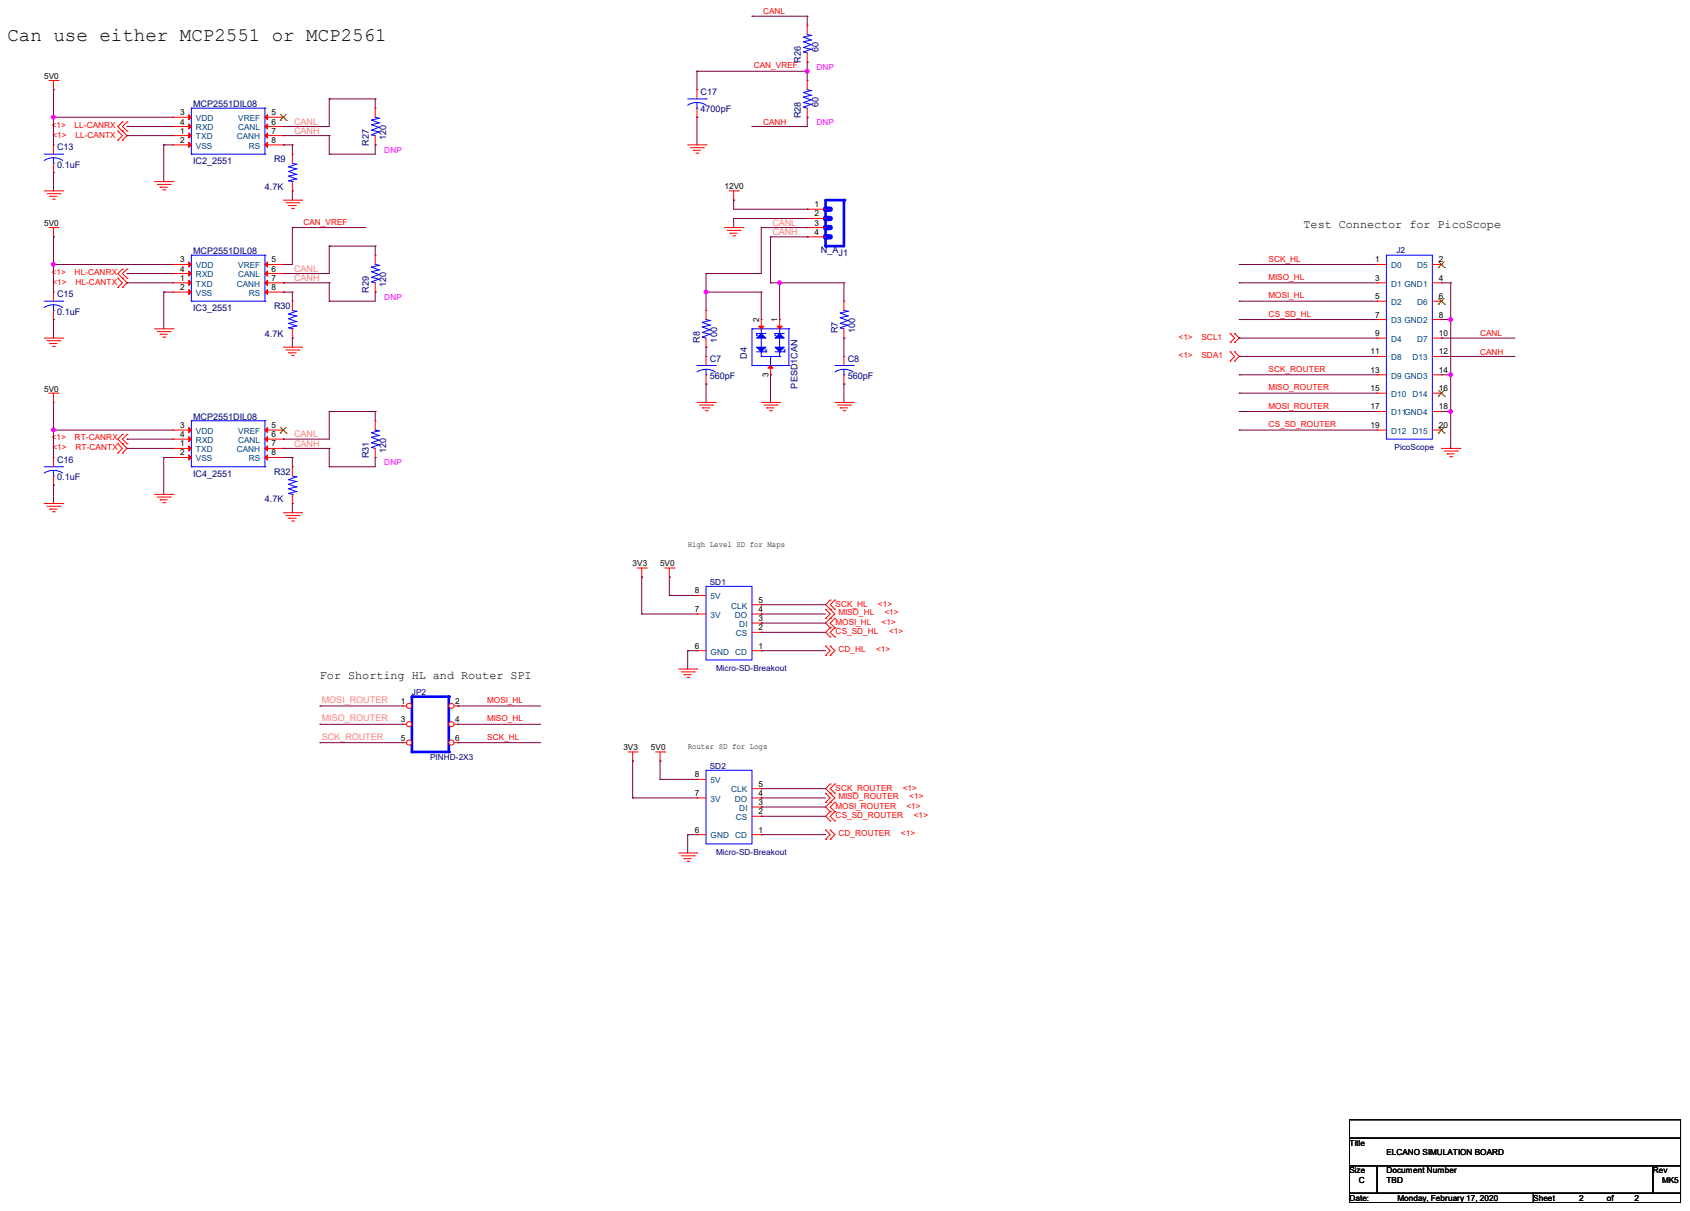
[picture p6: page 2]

Test Connector for PicoScope ¹²V0

High Level SD for Maps

For Shorting HL and Router SPI

Router SD for Logs

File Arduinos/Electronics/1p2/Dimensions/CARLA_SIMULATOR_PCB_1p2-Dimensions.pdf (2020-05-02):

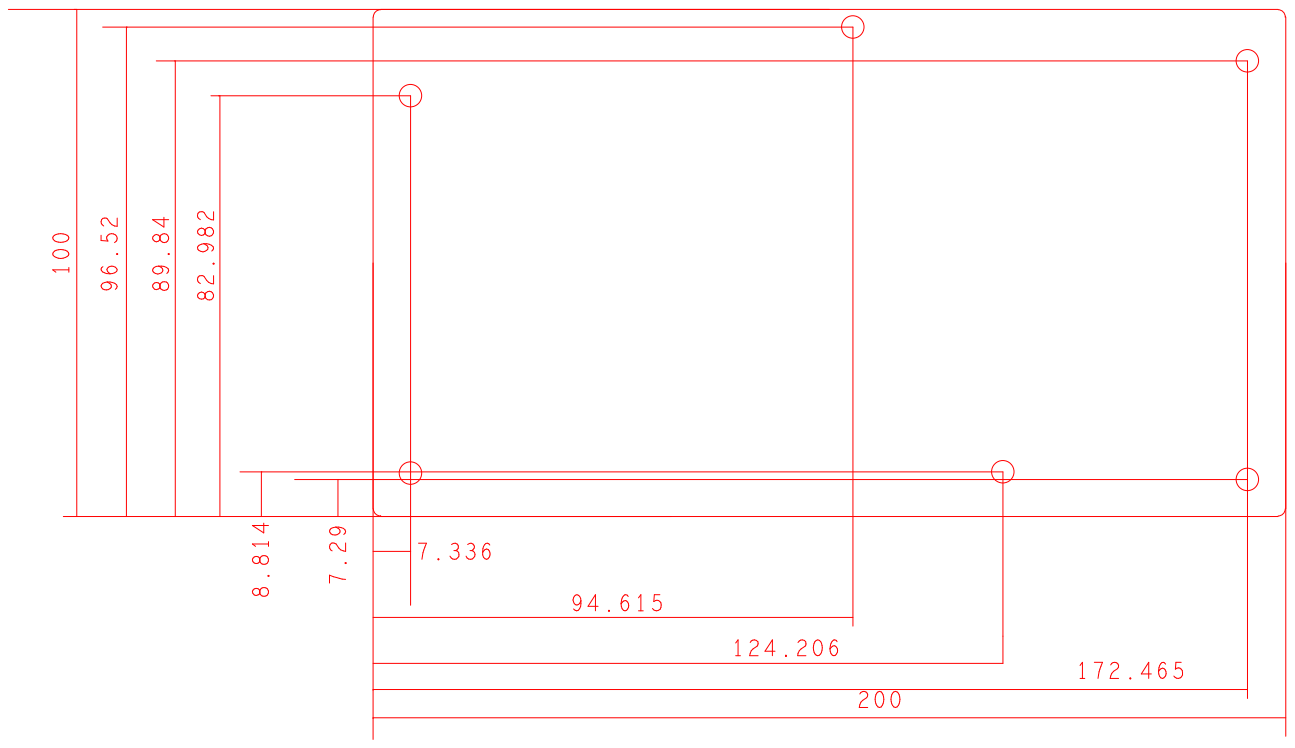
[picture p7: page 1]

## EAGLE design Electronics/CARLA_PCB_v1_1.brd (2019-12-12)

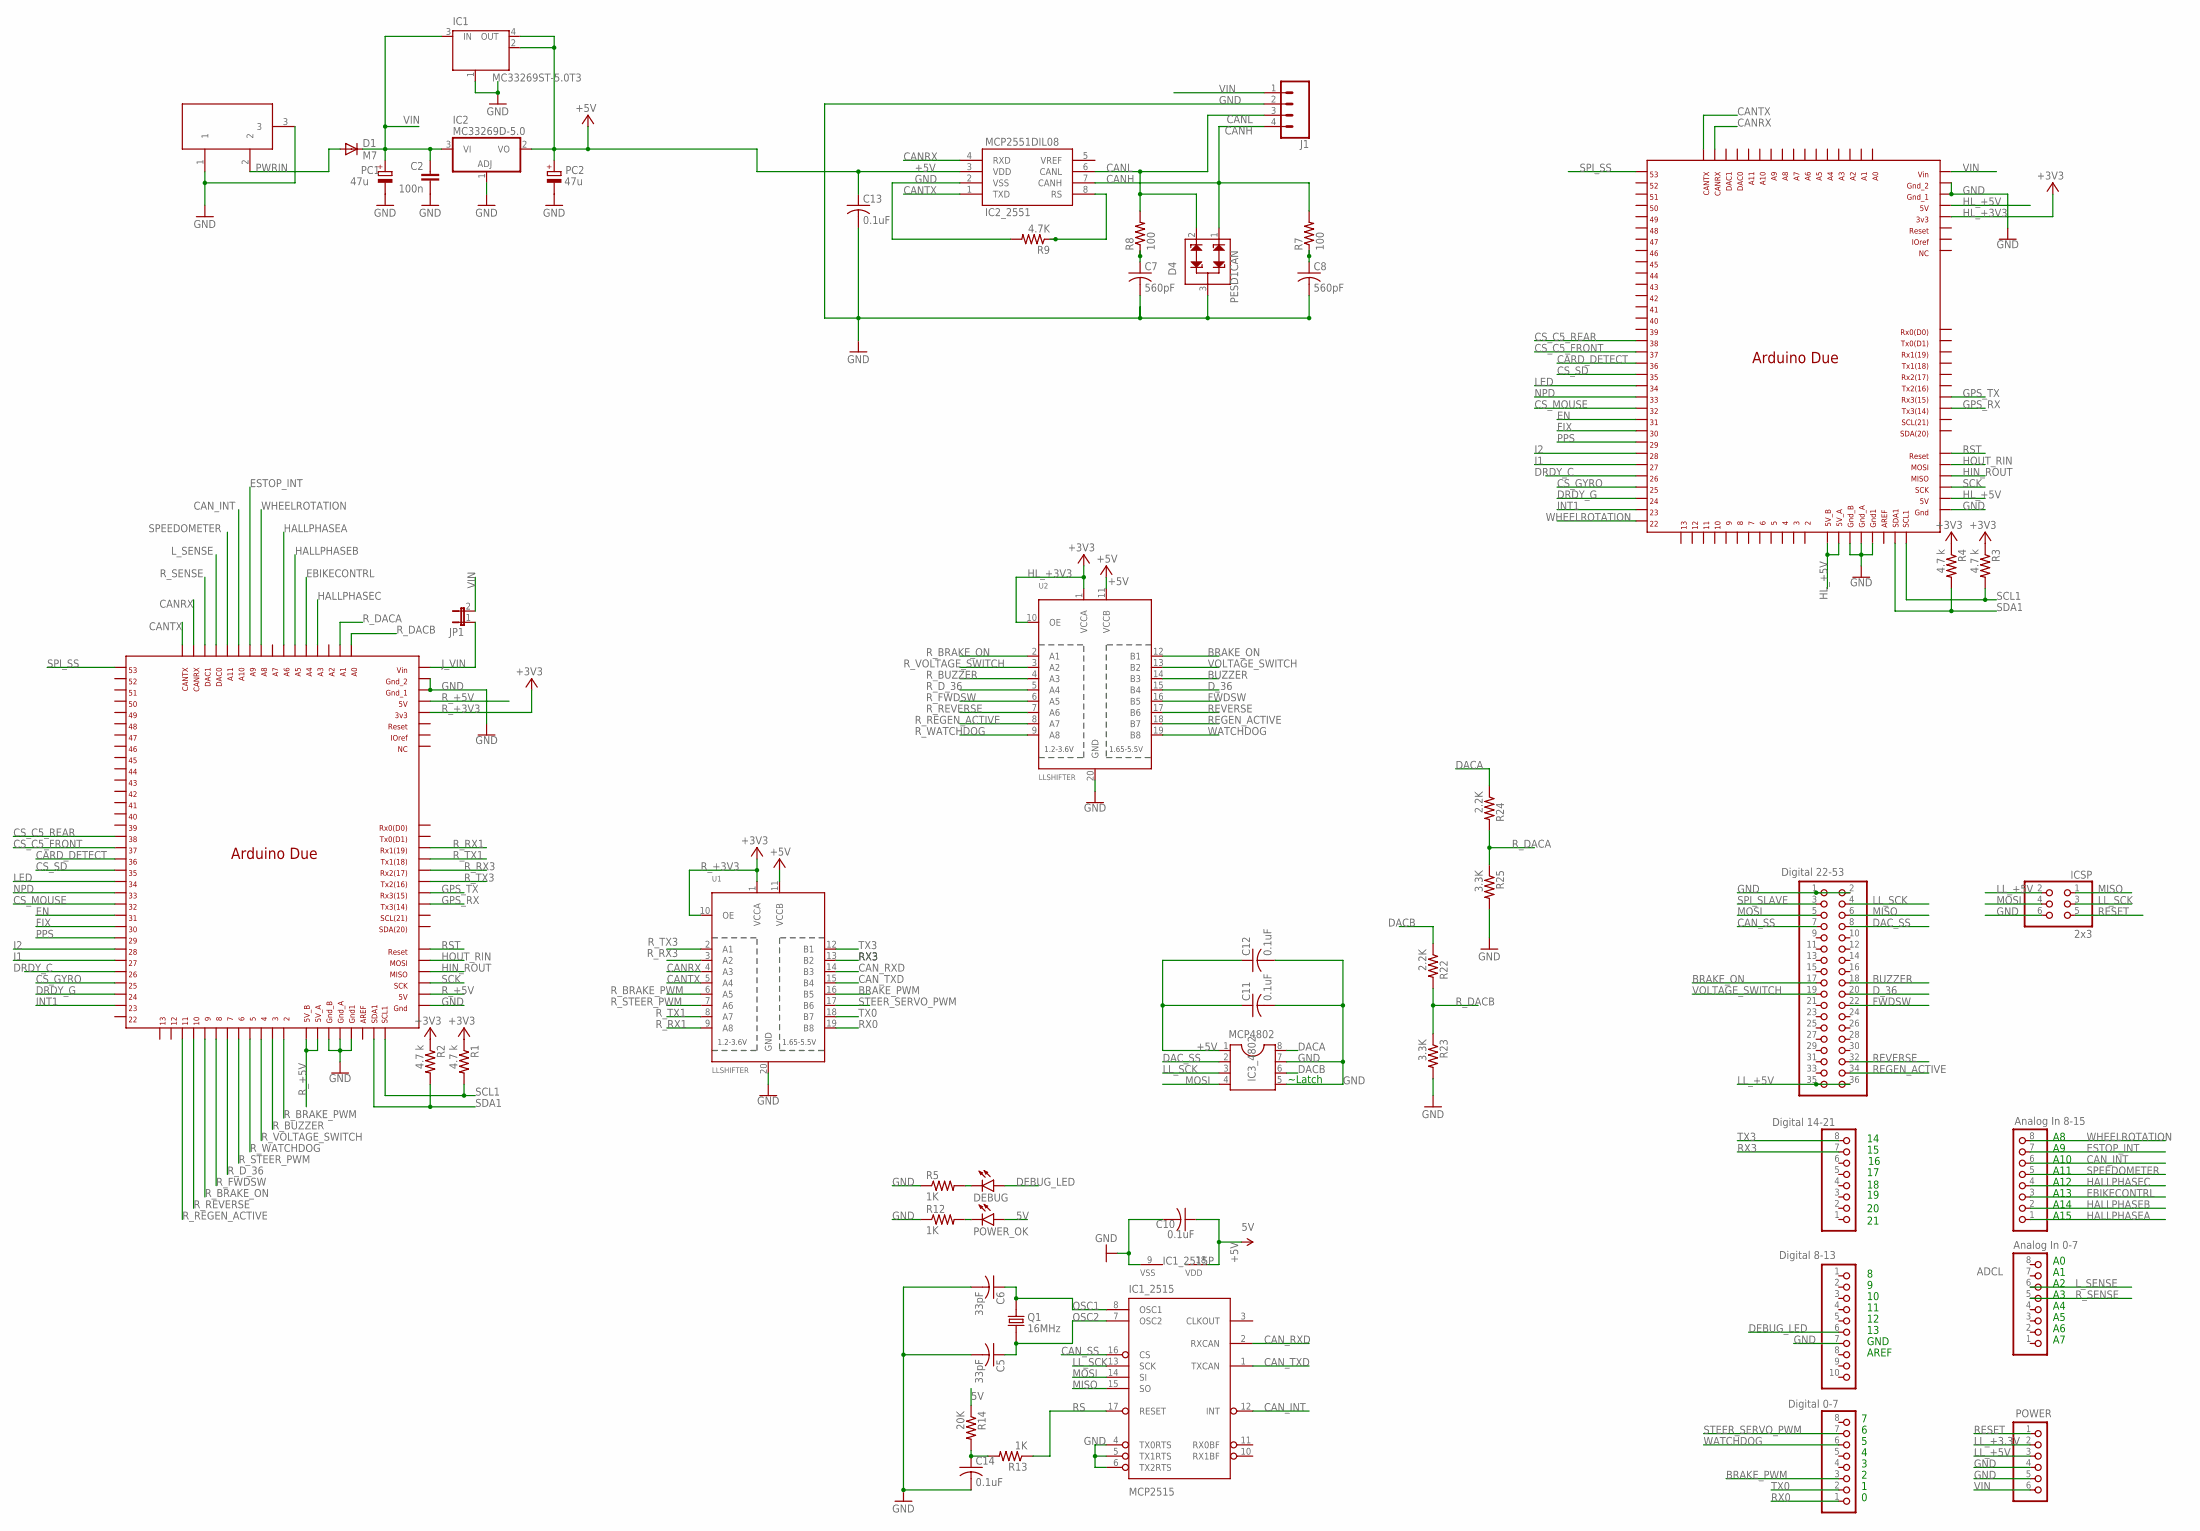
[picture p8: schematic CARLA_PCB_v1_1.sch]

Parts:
ADCH: Analog In 8-15; 1X08
ADCL: Analog In 0-7; 1X08
C2: 100n; C0603-ROUND
C5, C6: 33pF; C1206
C7, C8: 560pF; C1206
C10, C11, C12, C13, C14: 0.1uF; C1206
D1: M7; SMB
D4: PESD1CAN; SPARKFUN-DISCRETESEMI_SOT23-3
DEBUG: LED3MM
DIGITAL_0-7: Digital 0-7; 1X08
DIGITAL_8-13: Digital 8-13; 1X10
DIGITAL_14-21: Digital 14-21; 1X08
IC1: MC33269ST-5.0T3; SOT223
IC1_2515: MCP2515; DIP18
IC2: MC33269D-5.0; DPACK
IC2_2551: MCP2551DIL08; IC-PACKAGE_DIL08
IC3_4802: MCP4802; DIL08
ICSP: 2x3; 2X03
J1: CONN_04SCREW; SCREWTERMINAL-3.5MM-4
JP1: JP1E; JP1
MCU2, MCU3: DUE(NORMAL)
MEGA_EXPANSION: Digital 22-53; PINHEAD_2X18
PC1, PC2: 47u; PANASONIC_D
POWER: PINHD-1X6; 1X06
POWER_OK: LED3MM
Q1: 16MHz; XTAL_ECS-160-20-46X
R1, R2, R3, R4: 4.7 k; 0204/7
R5, R12, R13: 1K; R1206
R7, R8: 100; R1206
R9: 4.7K; R1206
R14: 20K; R1206
R22, R24: 2.2K; R1206
R23, R25: 3.3K; R1206
U1, U2: LLSHIFTER; ELSHIFTER
X1: DC21MMX; DC-21MM

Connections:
5V: POWER_OK.A, R14.1
+3V3: R1.1, R2.1, R3.1, R4.1
+5V: C10.1, C11.1, C12.1, C13.1, IC1.2 (OUT), IC1.4 (OUT), IC1_2515.18 (VDD), IC2.2 (VO), IC2_2551.3 (VDD), IC3_4802.1, PC2.+, U1.11 (VCCB), U2.11 (VCCB)
BRAKE_ON: MEGA_EXPANSION.17, U2.12 (B1)
BRAKE_PWM: DIGITAL_0-7.3, U1.16 (B5)
BUZZER: MEGA_EXPANSION.18, U2.14 (B3)
CANH: D4.1, IC2_2551.7 (CANH), J1.4, R7.2
CANL: D4.2, IC2_2551.6 (CANL), J1.3, R8.2
CANRX: IC2_2551.4 (RXD), MCU2.CANRX, MCU3.CANRX, U1.4 (A3)
CANTX: IC2_2551.1 (TXD), MCU2.CANTX, MCU3.CANTX, U1.5 (A4)
CAN_INT: ADCH.6, IC1_2515.12 (INT), MCU2.A10
CAN_RXD: IC1_2515.2 (RXCAN), U1.14 (B3)
CAN_SS: IC1_2515.16 (CS), MEGA_EXPANSION.7
CAN_TXD: IC1_2515.1 (TXCAN), U1.15 (B4)
CARD_DETECT: MCU2.36, MCU3.36
CS_C5_FRONT: MCU2.37, MCU3.37
CS_C5_REAR: MCU2.38, MCU3.38
CS_GYRO: MCU2.25, MCU3.25
CS_MOUSE: MCU2.32, MCU3.32
CS_SD: MCU2.35, MCU3.35
DACA: IC3_4802.8, R24.1
DACB: IC3_4802.6, R22.1
DAC_SS: IC3_4802.2, MEGA_EXPANSION.8
DEBUG_LED: DEBUG.A, DIGITAL_8-13.6
DRDY_C: MCU2.26, MCU3.26
DRDY_G: MCU2.24, MCU3.24
D_36: MEGA_EXPANSION.20, U2.15 (B4)
EBIKECONTRL: ADCH.3, MCU2.A4
EN: MCU2.31, MCU3.31
ESTOP_INT: ADCH.7, MCU2.A9
FIX: MCU2.30, MCU3.30
FWDSW: MEGA_EXPANSION.22, U2.16 (B5)
GND: C2.2, C5.2, C6.2, C7.2, C8.2, C10.2, C11.2, C12.2, C13.2, C14.2, D4.3, DIGITAL_8-13.7, IC1.1 (GND/ADJ), IC1_2515.4 (TX0RTS), IC1_2515.5 (TX1RTS), IC1_2515.6 (TX2RTS), IC1_2515.9 (VSS), IC2.1 (ADJ), IC2_2551.2 (VSS), IC3_4802.5, IC3_4802.7, ICSP.6, J1.2, MCU2.5V_ICSP, MCU2.GND1, MCU2.GND_1, MCU2.GND_2, MCU2.GND_A, MCU2.GND_B, MCU3.5V_ICSP, MCU3.GND1, MCU3.GND_1, MCU3.GND_2, MCU3.GND_A, MCU3.GND_B, MEGA_EXPANSION.1, MEGA_EXPANSION.2, PC1.-, PC2.-, POWER.4, POWER.5, R5.1, R9.2, R12.1, R23.2, R25.2, U1.20 (GND), U2.20 (GND), X1.1, X1.3
GPS_RX: MCU2.TX3, MCU3.TX3
GPS_TX: MCU2.RX3, MCU3.RX3
HALLPHASEA: ADCH.1, MCU2.A6
HALLPHASEB: ADCH.2, MCU2.A5
HALLPHASEC: ADCH.4, MCU2.A3
HIN_ROUT: MCU2.MISO_ICSP, MCU3.MISO_ICSP
HL_+3V3: MCU3.3V3, U2.1 (VCCA), U2.10 (OE)
HL_+5V: MCU3.5V, MCU3.5V_A, MCU3.5V_B, MCU3.GND_ICSP
HOUT_RIN: MCU2.MOSI_ICSP, MCU3.MOSI_ICSP
I1: MCU2.27, MCU3.27
I2: MCU2.28, MCU3.28
INT1: MCU2.23, MCU3.23
J_VIN: JP1.1, MCU2.VIN
LED: MCU2.34, MCU3.34
LL_+3.3V: POWER.2
LL_+5V: ICSP.2, MEGA_EXPANSION.35, MEGA_EXPANSION.36, POWER.3
LL_SCK: IC1_2515.13 (SCK), IC3_4802.3, ICSP.3, MEGA_EXPANSION.4
L_SENSE: ADCL.6, MCU2.DAC0
MISO: IC1_2515.15 (SO), ICSP.1, MEGA_EXPANSION.6
MOSI: IC1_2515.14 (SI), IC3_4802.4, ICSP.4, MEGA_EXPANSION.5
unnamed: C14.1, R13.2, R14.2
unnamed: C7.1, R8.1
unnamed: C8.1, R7.1
unnamed: POWER_OK.K (C), R12.2
unnamed: DEBUG.K (C), R5.2
unnamed: IC2_2551.8 (RS), R9.1
NPD: MCU2.33, MCU3.33
OSC1: C6.1, IC1_2515.8 (OSC1), Q1.2
OSC2: C5.1, IC1_2515.7 (OSC2), Q1.1
PPS: MCU2.29, MCU3.29
PWRIN: D1.A, X1.2
REGEN_ACTIVE: MEGA_EXPANSION.34, U2.18 (B7)
RESET: ICSP.5, POWER.1
REVERSE: MEGA_EXPANSION.32, U2.17 (B6)
RS: IC1_2515.17 (RESET), R13.1
RST: MCU2.RESET_ICSP, MCU3.RESET_ICSP
RX0: DIGITAL_0-7.1, U1.19 (B8)
RX3: DIGITAL_14-21.7, U1.13 (B2)
R_+3V3: MCU2.3V3, U1.1 (VCCA), U1.10 (OE)
R_+5V: MCU2.5V, MCU2.5V_A, MCU2.5V_B, MCU2.GND_ICSP
R_BRAKE_ON: MCU2.9, U2.2 (A1)
R_BRAKE_PWM: MCU2.2, U1.6 (A5)
R_BUZZER: MCU2.3, U2.4 (A3)
R_DACA: MCU2.A1, R24.2, R25.1
R_DACB: MCU2.A0, R22.2, R23.1
R_D_36: MCU2.7, U2.5 (A4)
R_FWDSW: MCU2.8, U2.6 (A5)
R_REGEN_ACTIVE: MCU2.11, U2.8 (A7)
R_REVERSE: MCU2.10, U2.7 (A6)
R_RX1: MCU2.RX1, U1.9 (A8)
R_RX3: MCU2.RX2, U1.3 (A2)
R_SENSE: ADCL.5, MCU2.DAC1
R_STEER_PWM: MCU2.6, U1.7 (A6)
R_TX1: MCU2.TX1, U1.8 (A7)
R_TX3: MCU2.TX2, U1.2 (A1)
R_VOLTAGE_SWITCH: MCU2.4, U2.3 (A2)
R_WATCHDOG: MCU2.5, U2.9 (A8)
SCK: MCU2.SCK_ICSP, MCU3.SCK_ICSP
SCL1: MCU2.SCL1, MCU3.SCL1, R1.2, R3.2
SDA1: MCU2.SDA1, MCU3.SDA1, R2.2, R4.2
SPEEDOMETER: ADCH.5, MCU2.A11
SPI_SLAVE: MEGA_EXPANSION.3
SPI_SS: MCU2.53, MCU3.53
STEER_SERVO_PWM: DIGITAL_0-7.7, U1.17 (B6)
TX0: DIGITAL_0-7.2, U1.18 (B7)
TX3: DIGITAL_14-21.8, U1.12 (B1)
VIN: C2.1, D1.C, IC1.3 (IN), IC2.3 (VI), J1.1, JP1.2, MCU3.VIN, PC1.+, POWER.6
VOLTAGE_SWITCH: MEGA_EXPANSION.19, U2.13 (B2)
WATCHDOG: DIGITAL_0-7.6, U2.19 (B8)
WHEELROTATION: ADCH.8, MCU2.A8, MCU3.22

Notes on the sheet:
A10
A11
A12
A13
A14
A15
GND
AREF
~Latch

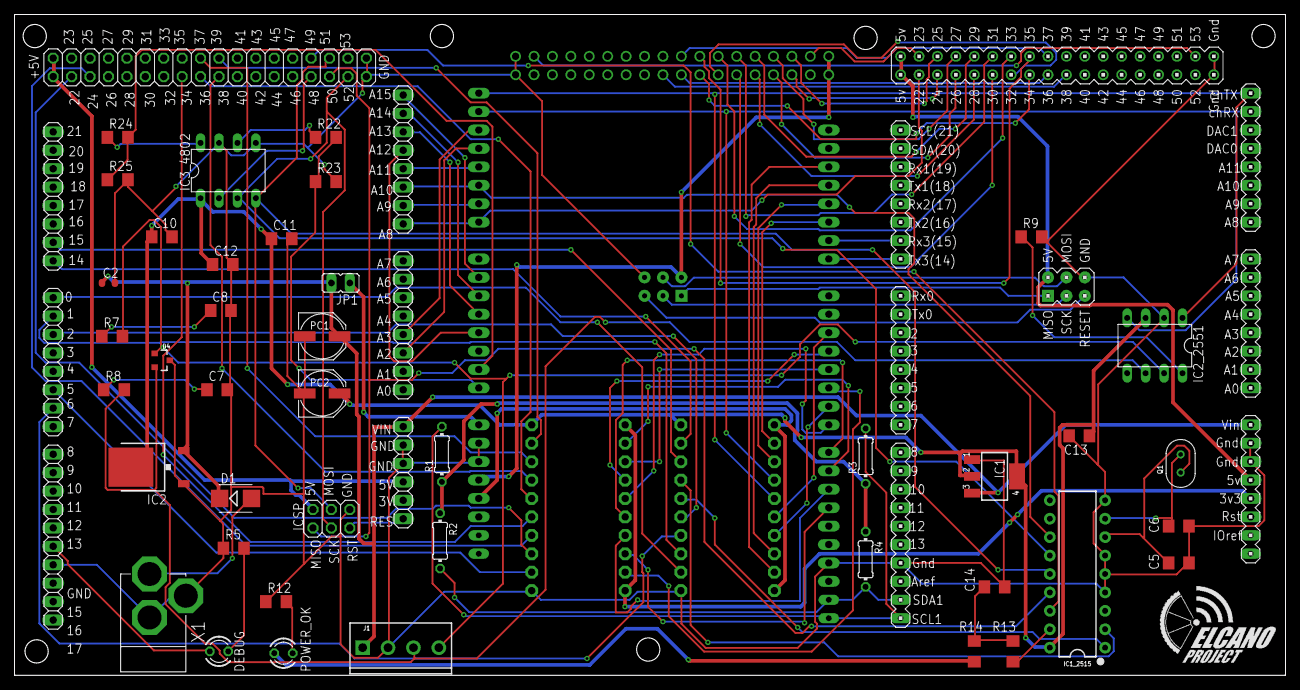
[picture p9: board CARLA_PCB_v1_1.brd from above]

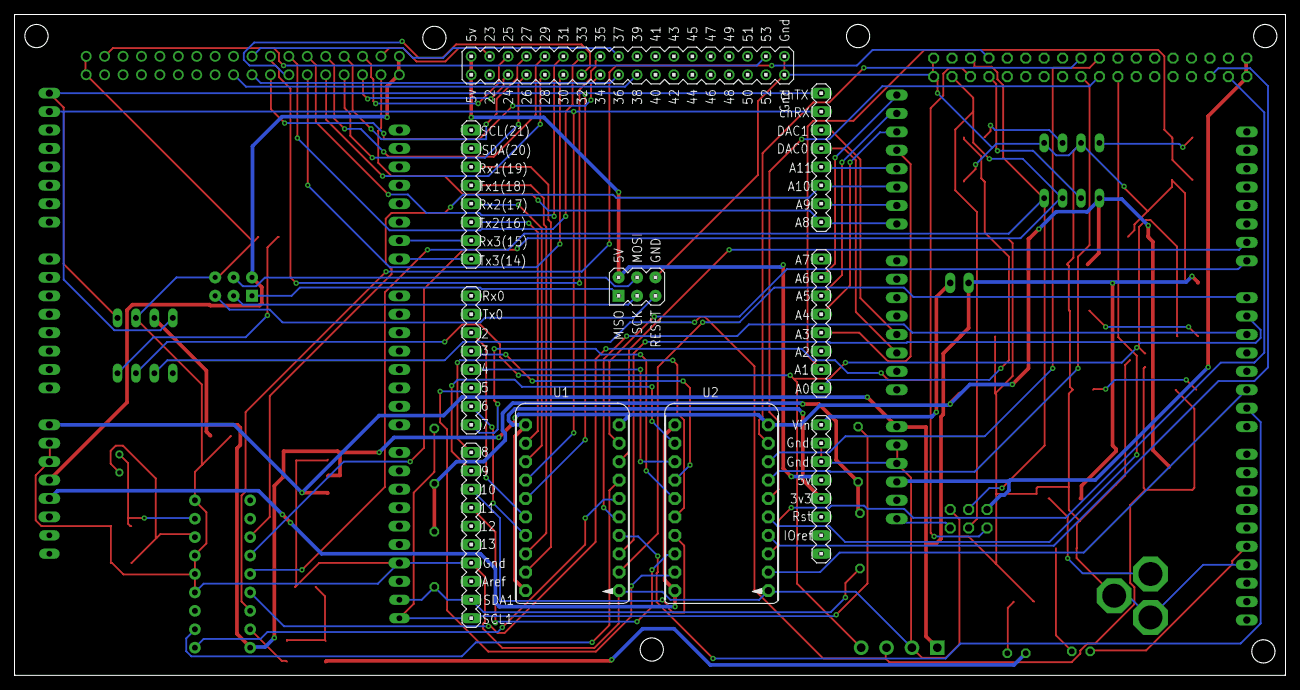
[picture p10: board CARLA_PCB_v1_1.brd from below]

Board: 2 copper layers, 175.2 x 91.1 mm, 52 parts (3 on the bottom side), 101 nets.

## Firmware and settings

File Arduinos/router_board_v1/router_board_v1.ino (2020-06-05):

/*
  Elcano Carla Simulator Capstone
  UW Bothell, 2020
  Advisor : Tyler Folsom
  Team : Team: Launnie Ginn, Willeta Song, Colton Sellers, Brandon Thompson, Mariah Files
  router_board.ino
  Version: 2.0
  The main purposes of this program are:
    - Route actuation controls from low-level to Carla
    - Route simulated sensor data from Carla to low/high Level
** Data being sent to Carla is in the format:
  {Header Byte}{Data Bytes}
  The number of data bytes is determined by the type of data being sent, which is defined by the header byte.

  Portions of GPS code based on information found here: https://ucexperiment.wordpress.com/2012/03/12/arduino-scripted-gps-simulator/

*/

#include "router.h"
#include <Wire.h>

// Download from github.com/ivanseidel/DueTimer
//  -Follow instructions on github page to put in Arduino library
#include "DueTimer.h"


// Ensure cyclometer clicked at least once before changing its frequency
bool clicked = true;
uint32_t velocityPulseTime;


// Used for receiving serial ascii messages
const byte numChars = 64;
char receivedChars[numChars];
boolean newData = false;
byte len = 0;
int receivedData = 0;


//Steering variables
volatile int pulseTime = 0;
volatile long streerTimerStart = 0;
byte steeringPrevious = 0;
byte steeringdebounce = 0;
bool inSteering = false;
byte steering = 0;


// Throttle Variables
volatile byte throttle = 0;
byte throttleSent = 0;

// Braking Variables
byte brake = 0;
bool inBraking = false;
bool brakeChange = false;

// Accelerometer and Magnetometer buffers
byte accelDataBuffer[ACCELBYTES];
byte magDataBuffer[MAGBYTES];

// Magnetometer flags
bool magRegMRead;
bool magRegMgRead;

// GPS Variables
char sec[2];
char lat[10];
char latdir[2];
char lng[11];
char lngdir[2];
char hdg[7];
char spd[7];
volatile uint8_t t4 = 10;
volatile uint8_t t3 = 30;
volatile uint8_t t2 = 0;
volatile uint8_t t1 = 0;
volatile boolean _1Hz_flag = 0;
char gprmc[96];


//Set pins, prepare serial.
void setup() {

  // Serial port used for debug
  Serial.begin(BAUDRATE);
  // Serial USB port used for Carla connection
  SerialUSB.begin(BAUDRATE);
  // Serial port for GPS
  GPSSERIAL.begin(GPSBAUD);

  //GPS variables initial loading
  _1Hz_flag = false;
  sec[0] = '0';
  sec[1] = '\0';
  lat[10] = '\0';
  latdir[1] = '\0';
  lng[11] = '\0';
  lngdir[1] = '\0';
  hdg[7] = '\0';
  spd[7] = '\0';


  // Built in built in LED for debug
  pinMode(LED_BUILTIN, OUTPUT);


  // Set pins
  pinMode(BRAKE_PIN, INPUT);
  pinMode(STEER_PIN, INPUT);
  pinMode(PULSE_PIN, OUTPUT);

  // Start cyclometer pulse with arbitrarily large value
  Timer3.attachInterrupt(sendPulse).start(MAXPULSETIME);

  // Setup I2C for accelerometer and Magnetometer
  // Currently only Magnetrometer is setup for heading data to high level
  // Need to develop emulation of multiple slave addresses on single bus.
  //Wire.begin(ACCELADDRESS);
  //Wire.onRequest(accelEvent);
  Wire.begin(MAGADDRESS);       // Accelerometer and magnetometer addresses
  Wire.onRequest(magEvent);  // register callback function for sending magnetometer data
  Wire.onReceive(magRegEvent); // Register callback for receiving commands for magnetometer

  // Wait until start msg from laptop
  while (SerialUSB.available() <= 0) {}
  SerialUSB.read(); // flush char in SerialUSB
  delay(100);   // Allow time for some data from Carla to be captured

  // Steering and braking handled in interrupts
  attachInterrupt(STEER_PIN, manageSteering, CHANGE);
  attachInterrupt(BRAKE_PIN, manageBrake, CHANGE);
}




/*
  TODO:
  - Move things to own functions.

*/
void loop() {
  receivedData = 0;

  //We don't need to adjust the throttle if we are braking.
  if (!inBraking) {
    // Read throttle and send to Carla if it has changed
    int throttleRead = analogRead(THROTTLE_PIN);
    throttle = throttleRead >> 2;  // Read with 8 bit resolution

    //only send throttle data to Carla if it is different.
    if (throttle > (throttleSent + THROTTLENOISEMASK) || throttle < (throttleSent - THROTTLENOISEMASK)) {
      throttleSent = throttle;
      sendToCarla(throttleCommand, &throttleSent, THROTTLEBYTES);
#if DEBUG
      Serial.print("Throttle: ");
      Serial.println(throttleSent);
#endif
    }
  }

  // If brake state has changed, send new brake and throttle values to Carla
  if (brakeChange) {
    sendToCarla(throttleCommand, &throttleSent, THROTTLEBYTES);
    sendToCarla(brakeCommand, &brake, BRAKEBYTES);
    brakeChange = false;
#if DEBUG
    Serial.print("Brake: ");
    Serial.println(brake);
#endif
  }

  // send steering data if it has been updated
  if (inSteering) {
    if (steeringdebounce == 0) {
      steeringdebounce = steering;
    } else if (steeringdebounce == steering) {
      sendToCarla(steerCommand, &steering, STEERBYTES);
      inSteering = false;
#if DEBUG
      Serial.print("Pulse Time = ");
      Serial.println(pulseTime);
      Serial.print("Steering: ");
      Serial.println(steering);
#endif
      analogWrite(R_SENSE, ((0xFF - steering) << 2));
      analogWrite(L_SENSE, (steering << 2));
      steeringdebounce = 0;
    } else {
      steeringdebounce = 0;
    }
  }

  // Receive data from Carla
  if (SerialUSB.available()) {
    volatile byte *receiveData = receiveFromCarla(1);
#if DEBUG
    Serial.println(receiveData[0]); //debug
#endif
    switch (receiveData[0]) {
      case accelCommand:
        // Get number of bytes associated with Accelerometer data
        receiveData = receiveFromCarla(ACCELBYTES);
        // Put received data into the accelerometer buffer
        loadAccelBuffer(receiveData);
        break;
      case gyroCommand:
        // Get number of bytes associated with gyroscope data
        receiveData = receiveFromCarla(GYROBYTES);
        // TODO: ADD FUNCTION FOR GYROSCOPE
        break;
      case magCommand:
        // Get number of bytes associated with magnetometer data
        receiveData = receiveFromCarla(MAGBYTES);
        // Put received data into the magnetometer buffer
        loadMagBuffer(receiveData);
        break;
      case gpsCommand:
        // Get number of bytes associated with gps data
        receiveData = receiveFromCarla(GPSBYTES);

        uint8_t i;
        /* No need to send different milliseconds.
                //time
                sec[0] = receiveData[0];
        */
        //latitude
        for (i = 0; i < 9; i++)
          lat[i] = receiveData[i];
        latdir[0] = receiveData[9];
        //longitude
        for (i = 0; i < 10; i++)
          lng[i] = receiveData[i + 10];
        lngdir[0] = receiveData[20];
        /* Not currently using speed or heading from GPS
                //speed
                for (i = 0; i < 6; i++)
                  spd[i] = receiveData[i + 20];
                //heading
                for (i = 0; i < 6; i++)
                  hdg[i] = receiveData[i + 26];
        */
        //Data read to send flag
        _1Hz_flag = true;
        break;
      case velocitycommand:
        // get velocity pulse timing from Carla
        receiveData = receiveFromCarla(VELBYTES);
        velocityPulseTime = ((receiveData[0] << 24) | (receiveData[1] << 16) | (receiveData[2] << 8) | receiveData[3]);
#if DEBUG
        Serial.print("Velocity Pulse Time received: ");
        Serial.println(velocityPulseTime);
#endif
        break;
      default:
        // if unknown code, flush serial bus data to ensure we aren't out of sync.
        while (SerialUSB.available() > 0) {
          receiveData = receiveFromCarla(1);
        }
        break;
    }

    //Send GPS data to high level board if it is available
    if (_1Hz_flag) {
      IncrementTime();
      //format $GPRMC sentence
      // Message format is: UMT time, A, Lat, Long, Speed, Heading, Date, Magnetic variation*Checksum
      sprintf(gprmc, "$GPRMC,%2.2u%2.2u%2.2u.000,A,%9s,%s,%10s,%s,000.0,000.0,080112,,S", t4, t3, t2, lat, latdir, lng, lngdir);
      //calculate and add checksum
      calcGPSCheckSum(gprmc);
      // Send for debug
#if DEBUG
      Serial.println(gprmc);
#endif
      // Send GPS data to high Level
      GPSSERIAL.println(gprmc);
      _1Hz_flag = false;
    }
  }

  if (clicked) {
    if (velocityPulseTime > MAXPULSETIME)
      velocityPulseTime = MAXPULSETIME;
    Timer3.attachInterrupt(sendPulse).start(velocityPulseTime);
    clicked = false;
  }
}

volatile byte * receiveFromCarla(int byteCount) {
  static volatile byte data[RECEIVEBUFFERSIZE];
  for (byte i = 0; i < byteCount; i++) {
    while (!SerialUSB.available()) {
      //wait for data to be available
    }
    data[i] = SerialUSB.read();
  }
  return data;
}



// Sends data to carla. Command list needs match command list on Carla side.
// Defined in router.h as an enumeration
void sendToCarla(carlaCommand mode, byte data[], int byteCount) {

  char sendData[byteCount];
  for (byte i = 0; i < byteCount; i++) {
    sendData[i] = data[i];
  }

  SerialUSB.write(mode);
  SerialUSB.write(sendData, byteCount);
}



// Load the Accelerometer buffer from the data received from Carla.
void loadAccelBuffer(volatile byte receiveData[]) {
  for (byte i = 0; i < ACCELBYTES; i++) {
    accelDataBuffer[i] = receiveData[i];
  }
  // after buffer is loaded, inform high level data is ready
  SETACCELINTERRUPT;
}



//Load the Magnetometer buffer from the data received from Carla.
void loadMagBuffer(volatile byte receiveData[]) {
  for (byte i = 0; i < MAGBYTES; i++) {
    magDataBuffer[i] = receiveData[i];
  }
  // after buffer is loaded, inform high level data is ready
  SETMAGINTERRUPT;
}

//Blink the on-board LED to test the cyclometer
void Blink() {
  digitalWrite(LED_BUILTIN, digitalRead(LED_BUILTIN) ^ 1);
}


/****************************************************************

                          GPS Functions

 ****************************************************************/

void IncrementTime() {

  t2++;
  if (t2 > 59) {
    t2 = 0;
    t3++;
  }
  if (t3 > 59) {
    t3 = 0;
    t4++;
  }
  if (t4 > 23)
    t4 = 0;
}

void calcGPSCheckSum(char *buff)
{
  char cs = 0;
  int i = 1;
  while (buff[i]) {
    cs ^= buff[i];
    i++;
  }
  sprintf(buff, "%s*%02X", buff, cs);
}

/****************************************************************

                          ISR ROUTINES

 ****************************************************************/

/* THE CYCLOMETER FUNCTION NEEDS TO BE REDEFINED TO MATCH THE NEW SCOPE
    Sends pulse to low level for speed calculation. Currently on random digital pin.  Has to be
  implemented for corresponding anaolog pin.*/

void sendPulse() {
  //noInterrupts();
  digitalWrite(PULSE_PIN, HIGH);
  digitalWrite(PULSE_PIN, LOW);

  clicked = true;

  // Debug
  Blink();
  //interrupts();
}


// Measured PWM frequency from Low level board is ~490Hz, So PWM signal is between 0 and 2040 us.
// Steering ISR, Interrupt on change.
void manageSteering() {
  //noInterrupts();
  //if the pin has gone HIGH, record the microseconds since the Arduino started up
  if (digitalRead(STEER_PIN) == HIGH)
  {
    streerTimerStart = micros();
  }
  //otherwise, the pin has gone LOW
  else
  {
    //only worry about this if the timer hasn't actually started
    if (streerTimerStart != 0)
    {
      //record the pulse time
      steeringPrevious = steering; // used to check if steering has changed.
      pulseTime = ((volatile long)micros() - streerTimerStart);
      steering = map(pulseTime, 900, 1950, 0, 255);
      if (steering != steeringPrevious)
        inSteering = true;
      //restart the timer
      streerTimerStart = 0;
    }
  }
  //interrupts();
}


// ISR for brake pin
void manageBrake () {
  if (digitalRead(BRAKE_PIN) == HIGH) {
    brake = 0xFF;  // Feel free to change
    throttleSent = 0;
    inBraking = true;
  }
  else {
    brake = 0;
    inBraking = false;
  }
  brakeChange = true;
}

/*
  // ISR for read from Accelerometer address
  void accelEvent() {
  Wire.write(accelDataBuffer, ACCELBYTES);
  CLEARACCELINTERRUPT;
  }
*/

// ISR for read from Magnetometer address
void magEvent() {
  if (magRegMRead) {
    Wire.write(0x10);  // Adafruit_LSM303_U driver expects to read 0x10 from this register
  } else if (magRegMgRead) {
    Wire.write(0x01);  // send data ready bit
  } else {
    Wire.write(magDataBuffer, MAGBYTES);
    CLEARMAGINTERRUPT;
  }
}

// ISR for a write command from the high level board on the I2C
void magRegEvent(int howMany) {
  char reg = Wire.read();
  switch (reg) {
    case LSM303_REGISTER_MAG_CRA_REG_M:
      magRegMRead = true;
      break;
    case LSM303_REGISTER_MAG_SR_REG_Mg:
      magRegMgRead = true;
      break;
    default:
      //if we receive something else, clear the flags
      magRegMRead = false;
      magRegMgRead = false;
      break;
  }
  while (Wire.available()) // clear buffer if this is a write command
  {
    char c = Wire.read(); // receive byte as a character
    //clear read flags because this is a write command
    magRegMRead = false;
    magRegMgRead = false;
  }

}

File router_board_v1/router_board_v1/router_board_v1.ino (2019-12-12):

'''

Elcano Carla Simulator Capstone
UW Bothell, 2019

Advisor : Tyler Folsom

Team : Team: Zach Gale, Jonah Lim, Matthew Moscola, Francisco Navarro-Diaz

router_board_v1.ino

Version: 1.0

The main purposes of this program are:
    - Route actuation controls from low-level to Carla
    - Route simulated sensor data from Carla to low/high Level


** Current implementation relies on order of sending to identify data

'''

#define PULSE_PIN 5
#define END_MARKER '@'  // char that signifies the end of a block of sensor data
#define BRAKE_PIN 6
#define STEER_PIN 9
#define THROTTLE_PIN A1

// Download from github.com/ivanseidel/DueTimer
//  -Follow instructions on github page to put in Arduino library
#include "DueTimer.h"

// Ensure cyclometer clicked at least once before changing its frequency
boolean clicked = false;

// Used for receiving serial ascii messages
const byte numChars = 64;
char receivedChars[numChars];
boolean newData = false;
byte len = 0;
int receivedData = 0;

int loopStart = 0;

// bool inSteering = false;
// int steeringRead = 0;
// int steerTime = 0;

// For formatting data to be sent to Carla
String nl = "\n";
String posdeci = "0.";
String negdeci = "-0.";

// These variables hold actuation data
String throttle = "0.0\n";
String brake = "0.0\n";
String steering = "0.0\n";

'''
Set pins, prepare serial.
'''
void setup() {
  Serial.begin(115200);
  SerialUSB.begin(115200);

  // Built in built in LED for debug
  pinMode(LED_BUILTIN, OUTPUT);

  // Set pins
  pinMode(BRAKE_PIN, INPUT);
  pinMode(STEER_PIN, INPUT);

  //Serial1.begin(9600);

  // Start cyclometer pulse with arbitrarily large value
  Timer3.attachInterrupt(sendPulse).start(2000000);

  // Initialize with no steering, brakes, or throttle
  setActuation(throttle, steering, brake);

  // Wait until start msg from laptop
  while (Serial.available() <= 0) {}
  Serial.read(); // flush char in serial
  delay(100);   // Allow time for some data from Carla to be captured
  loopStart = millis();

  //attachInterrupt(STEER_PIN, manageSteering, CHANGE);
}


'''
Each loop does 3 things
  - Reads actuation signals from low level board, updates last seen values.
  - Sends formatted actuation data to PC connected to Carla.
  - Retrieves simulated sensor data from the PC.
'''
void loop() {
  int start = millis();
  receivedData = 0;

  /////////////////////////////////////////////////
  // Update actuation instructions from low level
  //  Throttle : from 50 to 225 (After reading signal about 40 to 140), analogRead from pin A1
  //  Brake: on or off, digital pin 9
  //  Steering: Pulse width, digital pin 6
  //////////////////////////////////////////////////

  // Read throttle, convert.  Carla throttle values from 0.0 to 1.0
  //  Set throttle global var to a float from 0.0 1.0 as a String ending with new line
  int throttleRead = analogRead(THROTTLE_PIN);
  throttleRead = throttleRead >> 2;  // Read with 8 bit resolution
  // Temporary: map values to 0.1 to 0.9

  if (throttleRead >= 20) {
    throttleRead = map(throttleRead, 30, 140, 1, 9);
    if (throttleRead > 9) throttleRead = 9;
    throttle = posdeci + throttleRead + nl;
    //SerialUSB.println(throttleRead);
  }
  else throttle = "0.0\n";


  // Read brake, turn brake on or off.  Carla brake values from 0.0 to 1.0
  //  Set brake global var to a float from 0.0 1.0 as a String ending with new line
  if (digitalRead(BRAKE_PIN) == HIGH) {
    brake = "0.3\n";  // Feel free to change
    throttle = "0.0\n";
  }
  else brake = "0.0\n";
  //Serial.print(brake);
  
  steering = "0.0\n";
//  if (steeringRead = pulseIn(STEER_PIN, HIGH)) {
//      steeringRead = map(steeringRead, 1000, 1850, 0,18);
//      if (steeringRead < 0) {
//        if (steeringRead < -9) steeringRead = -9;  
//      }
//      steering = deci + steeringRead + nl;
//  }
//  else {
//    steering = "0.0\n";
//  }


  ///////////////////////////////////////
  // Send actuation control data to Carla
  ///////////////////////////////////////

  sendActuation();

  ////////////////////////////////////////////
  // Receive sensor data from Carla
  // Process data based on order received
  // Current order:
  //  1st) Wait time in between cyclometer pulse in seconds
  //  2nd) GPS data
  /////////////////////////////////////////////

  // Get time in between cyclometer pulse
  recvWithEndMarker();
  receiveNewData('s');

  // Get GPS data
  recvWithEndMarker();
  receiveNewData('g');

  /////////////////////////////////////////////////////
  // Finish data transactions
  /////////////////////////////////////////////////////

  // Make loop only happen once every 1/10th of a second
  while (millis() - start <= 100) {}

}

'''
Receives data from the programming port.
'''
void recvWithEndMarker() {
  static byte ndx = 0;
  char rc;

  while (Serial.available() > 0 && newData == false) {
    rc = Serial.read();

    if (rc != END_MARKER) {
      receivedChars[ndx] = rc;
      ndx++;
      if (ndx >= numChars) {
        ndx = numChars - 1;
      }

      len = ndx;
    }
    else {
      receivedChars[ndx] = '\0';  //Terminate string
      ndx = 0;
      newData = true;
    }
  }
}

'''
Does the appropriate action for each set of data retrieved
'''
void receiveNewData(char dataType) {
  if (newData == true) {
    // Identify type of data, process/route data appropriately

    // Data received is time (seconds) in between cyclometer pulse
    if (dataType == 's') {
      double waitTime = atof(receivedChars) * 1000000;  // in microseconds
      //SerialUSB.println(waitTime);
      if (waitTime > 0 && clicked) {
        Timer3.attachInterrupt(sendPulse).start(waitTime);
        clicked = false;
      }
    }

    // Data received is nmea GPS location of trike
    if (dataType == 'g') {
      SerialUSB.println(receivedChars);
      //Serial1.write(receivedChars, len);
    }

    // Clear receive buffer for new data
    newData = false;
    len = 0;
    receivedData++;
  }
}

'''
Allows you to set throttle, brake and steering in one call.
'''
void setActuation(String t, String s, String b) {
  throttle = t;
  brake = b;
  steering = s;
}

'''
Sends the last updated values for throttle, steering, and brakes.
'''
void sendActuation() {
  Serial.print(throttle);
  Serial.print(steering);
  Serial.print(brake);
}

'''
Sends pulse to low level for speed calculation.  Currently on random digital pin.  Has to be
implemented for corresponding anaolog pin.
'''
void sendPulse() {
  //noInterrupts();
  digitalWrite(PULSE_PIN, HIGH);
  digitalWrite(PULSE_PIN, LOW);

  clicked = true;

  // Debug
  Blink();
  //interrupts();
}

'''
Blink the on-board LED to test the cyclometer
'''
void Blink() {
  digitalWrite(LED_BUILTIN, digitalRead(LED_BUILTIN) ^ 1);
}

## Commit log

2019-11-27 CARLA Sim prototype files (microprocessor inadvertently flipped)
    [CARLA_PCB_v1_0.brd, CARLA_PCB_v1_0.sch]
2019-12-12 Please enter the commit message for your changes. Lines starting
    [BOM-CARLA-Sim-FinalDraft.xlsx, CARLA_PCB_v1_1.brd, CARLA_PCB_v1_1.sch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]
2020-02-11 Improve imports to work for debugging as well as contain all sensors in a package
2020-02-12 Steering implementation, moving to ISR
2020-02-12 Match schematic Pins
2020-02-12 Added Drive-By-Wire
    [LowLevelv3.brd, LowLevelv3.sch, Pin Mapping.xlsx]
2020-02-13 no interrupts during steering ISR added
2020-02-13 Drive-By-Wire Added
2020-02-13 This creates and implements the magnetometer, accelerometer, and gyroscope in its own .cpp. This will be implemented with the high level board to access the readings from the 3 sensors
2020-02-14 Update simulator.py
    Added an IMU sensor object to the vehicle actor, which will be used to find the accelerometer, magnetometer, and gyroscopic data from where it is attached on the vehicle
2020-02-17 sensor classes
2020-02-18 Arduino Control of Simulator Testing
2020-02-18 simulator.py is now driver of control between simulator and router
2020-02-19 Create readme.txt
    Previous version of simulator board. Eagle schematic and layout.
2020-02-19 Schematic MK5
    Schematic ported to Cadence. Corrected 5V/3V shorts. Added additional 2551's for CAN bus implementation. Corrected UART Rx/Tx connections. Added connector for PicoScope connection. Added SD cards for Router and High level boards.
    [CARLA_PCB_MK5.DSN]
2020-02-19 Layout MK5
    Ported to Cadence and updated to incorporate schematic changes.
    [CARLA_PCB_MK5.brd]
2020-02-19 Minor changes to test arduino
2020-02-19 Applying control requires previous throttle and brake
2020-02-19 Turn off camera lock for now
2020-02-20 Folder adjustments
    [CARLA_PCB_MK5.DSN, CARLA_PCB_MK5.brd, CARLA_PCB_v1_0.brd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]
2020-02-21 Simulator Board V1.2
    Connected second I2C bus between router and high level. Some routing and placement changes. Gerbers output.
    [CARLA_PCB_1p2.brd, CARLA_SIMULATOR_PCB_1p2.DSN]
2020-02-22 Steering Sensor on Simulation
2020-02-23 Added BOM
    Simulator Board BOM
    [Carla-Simulator-BOM-1p2.xlsx]
2020-02-23 Update Carla-Sim-1p2-Gerbers.zip
    Added Placement file to Gerbers
2020-02-23 Update CARLA_SIMULATOR_PCB_1p2.DSN
    Added info to schematic for BOM output
    [CARLA_SIMULATOR_PCB_1p2.DSN]
2020-02-26 Routerboard Interface class to carry out commands from board
2020-02-27 Sensor destruction fix
2020-03-05 Router board update
    Updated to match new Carla communication. Steering and braking are now interrupt driven. Added header file. Still need to do some code cleanup.
2020-03-11 Dimensional Drawings
    Added dimensional drawings
    [Carla_PCB_1p2.dxf, Carla_PCB_1p2_Dimensions.dxf]
2020-03-22 Receive from Carla Added
    Added functions for recieving data from Carla. Accelerometer and Magnetometer functions for sending to high level board over I2C are added. Currently using one I2C bus for each. Need to see if we can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
2020-04-23 Fix destruction of sensors
    [simulatedvehicle.py]
2020-04-24 Removal of Drive-By-Wire, will use its repo
    [LowLevelv3.brd, LowLevelv3.sch, Pin Mapping.xlsx]
2020-04-25 Move to arduino folder
    [CARLA_PCB_1p2.brd, CARLA_PCB_MK5.DSN, CARLA_PCB_MK5.brd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]
2020-04-28 Move files to arduino folder
2020-04-29 Brakes map to 0 to 1 in carla not -1 to 1
2020-05-01 Fix Param passing to simulator
    [start.py]
2020-05-01 Update ReadMe.md
    ReadMe to match current conditions of simulator repo. Huge overhaul since last change.
2020-05-08 Hot fix for host and port!
    [manual_control.py]
2020-05-19 Magnetometer Update
    Added code for magnetometer to be read from high level board.
    Magnetometer data from Carla should be 6 bytes in the format [xhi,xlo,zhi,zlo,yhi,ylo].
2020-05-19 add in world and HUD, still lots of issues tho!!!!
    [simulator.py]
2020-05-19 move camera to client, also clean up destruction
2020-05-19 create client class, move cameramanager
2020-05-20 doesn't require HUD anymore
    [simulatedvehicle.py]
2020-05-20 Implement GPS report thread
2020-05-21 Moved GPS thread down to end of function
2020-05-21 Fix to byte header
    [routerboard.py]
2020-05-21 Right to the correct serial for debug
    [router_board_v1.ino]
2020-05-23 Update to Magnetometer
    Updated flags for magnetometer write commands so correct data gets sent to high level.
    [router_board_v1.ino]
2020-05-23 beginning of compass thread
2020-05-23 Fix threading and add IMU
    [routerboard.py]
2020-05-23 fix closing of simulation
    [simulator.py]
2020-05-23 m/s velocity
2020-05-23 Velocity thread added
2020-05-28 Controller execution is handled by a thread within the controller class now.
2020-05-28 Add a pop up if no devices
2020-05-28 More threading
2020-05-31 routerboard.py update
    Decrease sleep time for recieving data from router board.
    Capture if speed is very small so calculation doesn't overflow the 32bit value.
    [routerboard.py]
2020-05-31 Routerboard update
    Added Steering reporting to low level.
    Added velocity pulses to the low level board.
2020-07-29 Fix throttle actuation

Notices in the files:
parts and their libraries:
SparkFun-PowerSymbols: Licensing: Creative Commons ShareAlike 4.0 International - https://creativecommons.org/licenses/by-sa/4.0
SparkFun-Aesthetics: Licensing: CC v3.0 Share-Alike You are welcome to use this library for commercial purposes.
